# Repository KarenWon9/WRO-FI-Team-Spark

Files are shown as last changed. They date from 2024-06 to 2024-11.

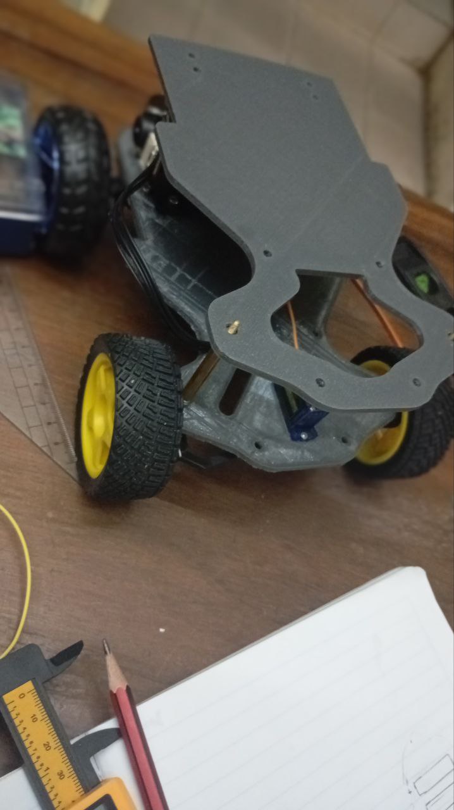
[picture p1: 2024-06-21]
other/First robot/Assembly.jpg

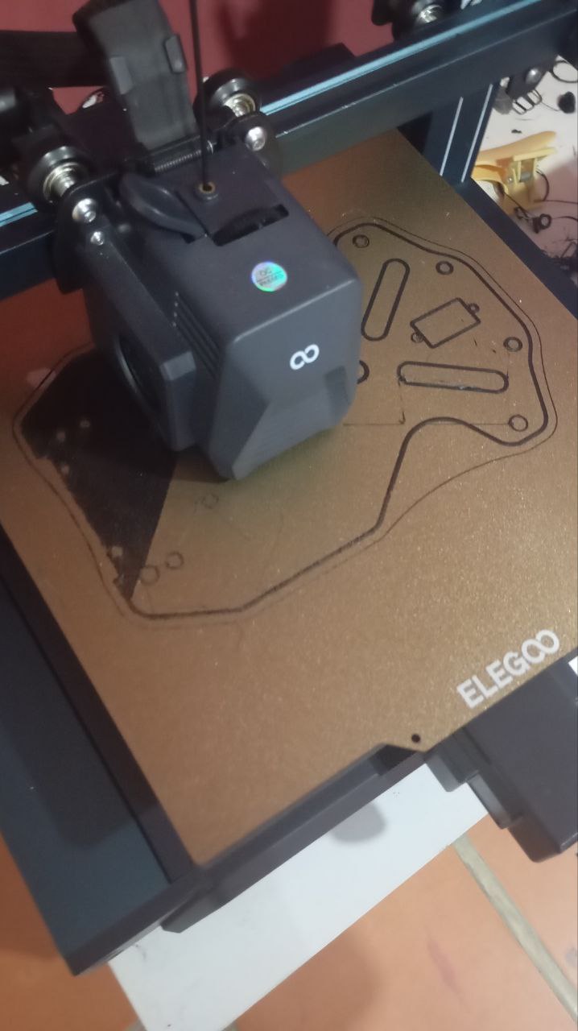
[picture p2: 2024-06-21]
other/First robot/Printig first chasis.jpg

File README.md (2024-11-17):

# Index

- 1.[ Introduction](#introduction)
    -
- 2.[ Components](#components)
    -
    - [Materials List](#materials-list)
    - [Arduino mega](#arduino-mega)
    - [Servo motor MG90S](#servo-motor-mg90s)
    - [Bridge H (L293N)](#bridge-h-l293n)
    - [Pixy2 cam](#pixy2-cam)
    - [Ultrasonic sensor (HC-S04)](#ultrasonic-sensor-hc-s04)
    - [Battery and charger](#battery-and-charger)
    - [Motor GA37-520](#motor-ga37-520)
    - [LM2596 HW-411 Step down](#lm2596-hw-411-step-down)

- 3.[ Robot floors](#robot-floors)
    -
    - [First and Second Floor](#first-and-second-floor)
        - [Front axel](#front-axle)
        - [Back axel](#back-axel)

    - [Third floor](#third-floor)
    - [Fourth floor](#fourth-floor)
        
- 4.[ 3D desing](models/)
    -
    - [Parts list](models/README.md#parts-list)
    - [Printing settings and recommendations](models/README.md#printing-settings-and-recommendations)
    - [STL files](models/stl/)
    - [Files ready to print](models/ready%20to%20print/)
    - [Full Chasis](models/Full%20chassis%20turkey.step)

- 5.[ Circuit diagram](schemes/README.md#circuit-diagram)<!--[Carpeta de Fuentes](../) asi se puede hacer un enlace con una carpeta -->
    -

- 6.[ Codes](src/)
    -
    - [Open challenge](src/Open%20challenge.ino)
    - [Closed challenge](src/Closed%20challenge.ino)

- 7.[ Flowcharts](src/README.md#flowcharts)
    -
    - [Open challenge](src/README.md#open-challenge)
    - [Closed challenge](src/README.md#close-challenge)
    
- 8.[ Vehicle photos](v-photos/README.md)
    -

- 9.[ Performance videos](video/README.md)
    -
    - [Open challenge](video/README.md#open-challenge)
    - [Closed challenge](video/README.md#closed-challenge)

- 10.[ Team photos](t-photos/)
    -
    - [Official photo](t-photos/README.md#official-photo)
    - [Funny photo](t-photos/README.md#funny-photo)

- 11.[ Annex](other/)
    -
    - [First robot](other/First%20robot/)
    - [Second robot](other/Scond%20robot/)
    - [Thirt robot - Final](other/Third%20robot%20-%20Final/)

<!---------------------------------------------espanol-------------------------------------------------------- -->

# Introduction 
Spark is a team from the Salto Angel School participating in the World Robot Olympiad 2024 (WRO) in the future engineers’ category. This team is comprised of three students: Victoria Saez, the new Captain who is in charge of the programming and electronic parts; Sebastian Salina, who is responsible for the designing and mechanical parts of the robot; and finally, Rosa Wong, who attends the documentation and is also a university student at Rafael Urdaneta University.

The World Robot Olympiad (WRO) is an event where young people from different parts of the world meet to show their knowledge and abilities in diverse categories. The future engineers' category is based on the creation of an autonomous robot capable of driving around a game field that measures 3m x 3m using obstacles in it or without them. Every year, the rules and challenges partially change and every four or five years represents a different challenge.

This report explains the components and parts of the robot built and designed by Team Spark to afford all the competition`s challenges.

# Components

## Materials List

| **Pieces** | **Quantity** |
|---|---|
| Arduino Mega | 1 |
| Pixy2 Cam | 1 |
| Ultrasonic Sensor (HC-SR04) | 3 |
| Bridge H L298N | 1 |
| Pull-up Button | 1 |
| Motor GA37-520 of 320rpm | 1 |
| Servo Motor MG90S | 1 |
| NI-MH Battery 12V 3000mAh | 1 |
| LM2596 HW-411 Step Down | 2 |
| Switch button | 1 |

## Arduino mega

(https://postimg.cc/2bnQkcR0)

| | | | |
| --- | --- | --- | --- |
| **Microcontroller** | ATmega2560 | **Operating Voltage** | 5V |
| **Input Voltage** | 7-12V | **Digital I/O Pins** | 54 (15 provide PWM output) |
| **Analog Input Pins** | 16 | **Flash Memory** | 256 KB |
| **SRAM** | 8 KB | **EEPROM** | 4 KB |

A unique controller, the Arduino Mega, was chosen to
manage all the robot`s functions. This model is distinguished
by its great prosecution capability inside the Arduino family,
letting it sort out complete code and manage a wide range of
components thanks to its large quantity of digital pins,
analogic, and PWM.

## Servo motor MG90S
(https://postimg.cc/4Y5NgpSp) 1-2-4-5-10-20pcs-MG90-S-Micro-Servo-Motor-Metal-Gear-Analog-RC-Servomotor-180-jpg.jpg (https://postimg.cc/SjMSKBPS)

| | | | |
| --- | --- | --- | --- |
| **Weight** | 13.4g  | **Operating speed**  | 0.1 s/60 degree, 0.08 s/60 degree (6V) 
| **Dimension** | 22.5 x 12 x 35.5 mm | **Operating voltage**| 4.8 V - 6.0 V |
| **Stall torque**  | 1.8 kgf·cm (4.8V), 2.2 kgf·cm (6V) | **Dead band width** | 5 μs |

It uses the servomotor MG90S in the turning system to get
precise turns. This model is smaller, lighter, and offers higher
torque than the SG90, which allows it to move the wheels with
the necessary strength for shunting, mainly in obstacle
evasion.

### Code

To make easier its use, we employed the library `<Servo.h>` and created a variable
called `SERVOPIN` where we put the pin that is in use, in this case, it is the 9.

``` ino
#include <Servo.h> // Library to control servomotors.

#define SERVOPIN 9 // Define the pin for the servomotor.

#define TURNGRADE 30 // Define the turning grades for the correct direction
#define CENTERVALUE 90 // Center value for the servomotor (straight).
#define MAXLEFT 156 // Top value towards the left for the servomotor.
#define MAXRIGHT 5 // Top value towards the right for the servomotor.

Servo direction; // Create an instance of the servomotor.

void center() {
  if (DEBUG) Serial3.println("Center"); // Print "Center" if DEBUG is active.
  direction.write(CENTERVALUE); // Place the servomotor in the central value (90 degrees).
}

void turnLeft() {
  if (DEBUG) Serial3.println("Left"); // Print "Left" if DEBUG is active.
  direction.write(MAXLEFT); // Turn the servomotor at the top to the left.
  direction.write(MAXLEFT); // Repeat the writing with precision.
  setMove(500, 1, TURNSPEED); // Perform the movement with 500 ticks in direction1 (forward) to TURNSPEED.
  center(); // Center the servomotor after the turning.
  stop(); // Stop the movement.
}

void turnRight() {
  if (DEBUG) Serial3.println("Right"); // Print "right" if DEBUG is active.
  direction.write(MAXRIGHT); // Turn the servomotor at the top to the right
  direction.write(MAXRIGHT); // Repeat the writing with precision.
  setMove(760, 1, MAXSPEED); // Perform the movement with 760 ticks in direction1 (forward) to MAXSPEED.
  center(); // Center the servomotor after the turning.
  stop(); // Stop the movement.
}

void turnGrade(int grade) {
  if (DEBUG) Serial3.println("turnGrade " + String(CENTERVALUE + grade)); // Print the calculated turn angle.
  direction.write(CENTERVALUE + grade); // Adjust the servomotor angle according to the specify grade.
}

```

This servomotor is used the whole time to perform the turnings that are required
during the challenges.

## Bridge H (L293N)
(https://postimg.cc/zyyJFzjQ)

| | | | |
| --- | --- | --- | --- |
| **Number of outputs**  | 4  | **Output current per channel**  | 2A - 3A peak|
| **Working voltage** | 5V to 35V  | **Current consumption (logical)** | 36mA  |

The L293N acts as an entrepreneur between the Arduino Mega and the motor, translating the instructions into movements. Its power to manage high voltages lets us use motors with nominal voltage, without limiting the controller voltage, which increases the efficiency and potential of the robot.

## Pixy2 cam
(https://postimg.cc/Jysw2JVr)

| | | | |
| --- | --- | --- | --- |
| **Procesador** | NXP LPC4330, 204 MHz, dual core | **Imagen sensor** | Aptina MT9M114, 1296×976 |
| **Field of view horizontaL** | 60° | **Field of view vertical** | 40° |
| **Operating current** | 140 mA | **Operating voltage** | USB (5V) o 6V a 10V |
| **RAM** | 264Kb | **Flash** | 2Mb |
| **Buses** | UART serial, SPI, I2C, USB, digital, analog | **Light** | 20 lumens approx |

The camera is capable of detecting seven colors
simultaneously. It is equipped with an internal processor,
which lets us explore just the necessary information for the
Arduino or other controllers due to the variety of connections
that allow it. Moreover, it counts with an obturation speed of 60 fps, an excellent gap, and white adjustable LED lights;
thus, the continuous movement and the lower light don’t
represent a huge problem.

### Code

#### Open challenge
With the camera connected to the pins I2C of the Arduino Mega add the library
`<Pixy2.h>`. we create a variable called `firstColorDetected` to save the first color that
is detected and apart a variable called `colorDetected` to indicate if any color is
detected. To start the camera pixy2 uses a `pixi.init()`, in the light of an additional
light is needed for the perception of the colors we will implement the
`pixy.setLamp(1, 0)` command, this will activate the camera LED lights.

``` ino
#include <Pixy2.h> 

Pixy2 pixy; // Create an object of the Pixy2 camera.

byte firstColorDetected = NONE; // Variable to save the first detected color.
bool colorDetected = false; // Indicate if a color is detected.

void flash(byte time) { //Function for indicating that the start button can be pressed 
  for (byte i = 0; i < time; i++) {
    pixy.setLamp(1, 0); // turn on the Pixy2 camera LED. 
    delay(200); // Delay 200 ms
    pixy.setLamp(0, 0); // turn off the Pixy2 camera LED
    delay(200); // Delay 200 ms
  }
}
In the case of the first color detected is blue which is assigned previously as 1, calls the function turnLeft.

           if (pixy.ccc.numBlocks > 0) { // if the Pixy detects an object
      stop(); // Stop the robot
      center(); // Center the servomotor.
      switch (pixy.ccc.blocks[0].m_signature) { // Depending on the signature of the object.
        case BLUE: // If detect a blue object.
          Serial3.println("BLUE"); // Print "BLUE" in the serial monitor.   
          if (!colorDetected) { // if any color has not been detected previously.
            colorDetected = true; // Mark color detected
            firstColorDetected = BLUE; // Stablish the color detected as blue.
          }
          if (colorDetected && firstColorDetected == ORANGE) { // if orange has already been detected.
            Go to orange; // Jump to the orange color section.
          }
Blue: // Tag the blue object.
          center(); // Center the servomotor
          readDistance(currentPosition); // Update 'currentPosition'
          readDistance(lastPosition); // Update 'lastPosition'
          while ((currentPosition[3] < 100)) { // While the left distance is less than 100 cm
            followLine(SPEED2); // Follow the wall to 'SPEED2'.
            readDistance(currentPosition); // Update 'currentPosition'
          }
         turnLeft(); // Turn to the left
          moveCM(40, 1, MAXSPEED); // Move the robot 40 cm forward to high-speed. 
          do {
            followLine(MAXSPEED); // Follow the inner walls to top-speed
            readDistance(currentPosition); // Update 'currentPosition'
          } while (currentPosition[3] > 100); // Repeat while the left distance is more than 100 cm
          break;

```

In the case of the first color detected being orange, assign it as 2 in the camera, and call the turnRight function.

``` ino
 case ORANGE: // If detect an orange object.
          Serial3.println("ORANGE"); // Print "ORANGE" in the serial monitor
          if (!colorDetected) { // If any color has not been detected previously.
            colorDetected = true; // Mark color detected
            firstColorDetected = ORANGE; // Stablish the first color detected as orange 
          }
          if (colorDetected && firstColorDetected == BLUE) { // If blue has already been detected.
            go to blue; // Jump to the blue color section. 
          }
Orange: // Tag the orange object.
          center(); // Center the servomotor.
          readDistance(currentPosition); // Update 'currentPosition'
          readDistance(lastPosition); // Update 'lastPosition'
          while ((currentPosition[2] < 100)) { // while the right distance is less than 100 cm
            followLine(SPEED2); // Follow the inner wall to 'SPEED2'
            readDistance(currentPosition); // Update 'currentPosition'
          }
          turnRight(); // Turn to the right.
          moveCM(40, 1, MAXSPEED); // Move the robot 40 cm forward to high-speed.
          do {
            followLine(MAXSPEED); // Follow the inner Wall to top-speed. 
            readDistance(currentPosition); // Update 'currentPosition'
          } while (currentPosition[2] > 100); // Repeat while the right distance is more than 100 cm
          break;
      }

```

## Ultrasonic sensor (HC-S04)
(https://postimg.cc/FYLFY2zg)

| | | | |
| --- | --- | --- | --- |
| **Operating voltage** | 5 V  | **Operating current** | 15mA |
| **Minimum range** | 2cm  | **Max. distance**  | 4m |
| **Measuring angle** | 15°  | **Output Echo signal**  | 40Hz |
| **Input Trigger signal**  | Input 10μs TTL | **Pulso Echo** | Output 100-25000 μs TTL |

The ultrasonic sensors are essential in our robot because
let's calculate distances by using ultrasonic vibes. These
sensors own a transmitter that sends the vibe and a receiver
to detect the echo of the reflexive vibes which lets us
determine the distance by the time it takes to come back with
a maximum detection of 4 meters, these sensors are ideal for
the game field size, which measures 3m x 3m. thanks to
them, the robot has a higher perception of its position and
anticipate possible coalitions effectively.

### Code

 To facilitate the frequency conversion of the Vibes reception in cms, use the library `<Ultrasonic.h>` and subsequently, define each sensor pin with Ultrasonic and the name given to the sensor followed by the (Trig, Echo).
``` ino
#include <Ultrasonic.h> // Library to manage ultrasonic sensors.
#define USTRIGHT A13 // Define the signal pin for the right ultrasonic sensor.
#define USERIGHT A12 // Define the echo pin for the right ultrasonic sensor.
#define USTLEFT A14 // Define the signal pin for the left ultrasonic sensor.
#define USELEFT A15 // Define the echo pin for the left ultrasonic sensor.

Ultrasonic USRight(USTRIGHT, USERIGHT); // Instance for the right ultrasonic sensor.
Ultrasonic USLeft(USTLEFT, USELEFT); // Instance to for left ultrasonic sensor.

int firstPosition[4]; // Array to upload the first position detected. 
int lastPosition[4]; // Array to upload the last position detected.
int currentPosition[4]; // Array to upload the current position detected.
int tempPosition[4]; // Array to upload the temporary position detected.

void readDistance(unsigned int* array) {
  array[2] = USRight.read(); // Upload the distance measure by the right ultrasonic sensor.
  array[3] = USLeft.read(); // Upload the distance measure by the left ultrasonic sensor.
}
```

Considering the values of the firstPosition, lastPosition, currentPosition and tempPosition, the robot does an angle correction to evade collisions both with the outer and inner wall staying centered.

``` ino
if (DEBUG2) printDistance(currentPosition); // Print the distances if DEBUG2 is active.
  if (tempPosition[2] < tempPosition[3]) { // If the right distance is less than the left position
    grade = map(currentPosition[2], tempPosition[2] - LMIN, tempPosition[2] + LMIN, TURNGRADE, -TURNGRADE); // Map the angle correction to the right.
    if (DEBUG) Serial3.println("1 Actual: " + String(currentPosition[2]) + ". Inicial: " + String(tempPosition[2])); // Depuration
  } else { // If the left distance is less or equal to the right 
    grade = map(currentPosition[3], tempPosition[3] - LMIN, tempPosition[3] + LMIN, -TURNGRADE, TURNGRADE); // Map the angle correction to the left.
    if (DEBUG) Serial3.println("2 Actual: " + String(currentPosition[3]) + ". Inicial: " + String(tempPosition[3])); // Depuration
  }
 if (DEBUG) Serial3.println("Grades : " + String(grade)); // Print the angle calculated correction.
  if (grade > TURNGRADE) { // Limit the higher turning angle.
    grade = TURNGRADE;
  } else if (grade < TURNGRADE * -1) { // Limit the lower turning angle
    grade = -TURNGRADE;
  }

```

## Battery and charger
(https://postimg.cc/pmzxWzcs) (https://postimg.cc/qgqTt9Zh)

| | | | |
| --- | --- | --- | --- |
| **Voltage**  | 12V  | **Capacity** | 3000mAh  |
| **Weight** | 567g | **Connector** | XT30 |
| **Replaceable Fuse** | 20A ATM | | |

After an extensive period of using NI-MH Batteries, we
have chosen a 12V battery and 3000 mAh Rev Robotics. This
new battery offers significant advantages.

Firstly, it gives better autonomy, letting the robot work
through longer periods without the charging needs. Its 12
voltages are enough to completely provide the energetic
needs of the robot, ensuring a favorable performance.

In addition, the battery includes a versatile charger with
two charging modes; a lower one (0.9 A) and a faster one (1.8
A), allowing flexibility in the time charging. Also, it is allowed
on international trips by airplane because it is made with
nickel which is safe for its transport.

Lastly, it is a prefabricated battery and offers a superior
level of security and efficiency as compared to the settings of
individual batteries.

## Motor GA37-520
(https://postimg.cc/xcWJpGb5) 

| | | | |
| --- | --- | --- | --- |
| **Nominal voltage**  | 12V | **Rated power** | 8,3W |
| **Rated current**| 1,5A | **Reduction** | 18.8:1  |
| **No-load speed** | 320rpm | **Rated speed**| 224rpm  |
| **No-load current** | ≥120mA | **Rated current**  | ≥400mA |
| **Rated torque** | 3.1Kg.cm  | **Par nominal**  | 0.67Kg.cm |

From a robotic kit, we have obtained two motors. Each one
to 12V, they are capable of going at a nominal speed of
250rpm and a 3,5 kg torque. Therefore using just a 12V motor
is enough to give it the speed, control, and attraction needed,
as well as greater management thanks to its encoder which
Let us have better precision in the turns that the robot should
do in the game field.

### Code

#### Open challenge

Firstly, we defined the variables that go in the H bridge and at
the same time connected the motor that is called `IN1` and IN2,
equally, we defined 3 different speeds (`MAXSPEED`,
`TURNSSPEED`, `SPEED2`) that could be inside of a range
between 255 and 0.

``` ino
#define IN1 4 // Define IN1 to the motor control pin.
#define IN2 5 // Define IN2 to the motor control pin.

#define MAXSPEED 250 // Top-Speed of the motor.
#define TURNSPEED 180 // Turnings Speed.
#define SPEED2 140 // Secundary Speed.

void stop() {
  if (DEBUG) Serial3.println("Stop"); // Print "Stop" in the serial monitor if the mode depuration is active.
  digitalWrite(IN1, LOW); // Turn off the motor in the IN1 direction.
  digitalWrite(IN2, LOW); // Turn off the motor in the IN2 direction.
}

void forward(byte speed) {
  if (DEBUG2) Serial3.println("Forward " + String(speed)); // Print "Forward" and the speed if DEBUG2 is active.
  analogWrite(IN1, speed); // Assign the speed in IN1 to go forward.
  digitalWrite(IN2, LOW); 
}
void backward(byte speed) {
  if (DEBUG) Serial3.println("Backward " + String(speed)); // Print "Backward" and the speed if DEBUG is active.
  digitalWrite(IN1, LOW); // turn off IN1 to return
  analogWrite(IN2, speed);

}
```

## LM2596 HW-411 Step down
(https://postimg.cc/LYcFFskc)

| | | | |
| --- | --- | --- | --- |
| **Input** | 4.5-40VDC | **Output** | 1.5-35VDC |
| **Rated Current** | 2A (Surge 3A) | **Regulation** | 0.5% |

To protect the robot`s electronic components from
possible damages caused by higher voltages that are not
required, for this, we have incorporated a voltage regulator in
our system. This device assures a constant and stable energy
supply, which prevents failures in the components, and also
increases the stability and movement of the robot in its
performance.

# Robot floors
The robot is made up of four floors
listed from button to top.

## First and Second Floor
Both floors are connected themselves including the Steering system and the Driving
system.

### Front Axle
The front axle of our robot is located in a steering system boosted by a servo
(Mg90s). this system counts with two wings, a superior one and a lower one, that
allow an appropriate Caster, between the wings we can find the pivots that count
with two bearings that facilitate the free movement of the wheels and avoid an
incorrect Camber, both pivots include a steering arm which is connected through
the Tie Rod.

Movement transmission is carried out by the servo connected to the Tie Rod. This
is connected at the same time with the Steering Arm of the right Wheel to make the
movement transmission we use the Steering Linkage that is connected to the left
steering arm. The Tie Rod has a screw thread which allows an adjustable Toe. The
tire rod and the steering linkage count with the rod end at the ends give us a wide
work range. making it much easier to integrate the servo with the steering system.

### Back Alxe
In the back of the robot, we can find the driven system (the wheels and the motor).
This motor transmits the movement through a chain and two sprockets a small one
with 10 teeth that is connected to the shaft and the bigger one with 15 teeth which
is connected to the motor. in this setting the velocity increases x1.5, resulting in a
rated speed of 540RPM. also, the ring for the wheels was modified to fit with a
5mm hexagonal shaft, which makes the movement transmission and the assembly
easier.

## Third Floor.
On the third floor, the robot has different electronic components that are essential. It is located the battery which provides the needed energy to the proper function of the robot. As well as the camera that let get images and detect obstacles. Besides, the ultrasonic sensors and the laser sensor are included, and each one sets in its respective support that helps with its positioning and functioning.

## Fourth floor.
On the fourth robot`s floor is located the controller and near it the shield, which organizes all the electric connections, including the feeding. The connections are soldered, avoiding accidental disconnection, and minimizing the errors and accidents during the robot's manipulation.

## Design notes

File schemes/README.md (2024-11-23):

# Circuit diagram
(https://postimg.cc/Mf2J6gyz)

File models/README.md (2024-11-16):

# 3D desing

## Parts list
| Peace | Total |
|---|---|
| Front ring | 2 |
| Back ring | 2 |
| Pivot | 2 |
| Pivot shaft | 2 |
| Ultrasonic case pt1 | 2 |
| Ultrasonic case pt2 | 2 |
| Flexible wings | 2 |
| Pixy base | 1 |
| Laser sensor case pt1 | 1 |
| Laser sensor case pt2 | 1 |
| Chasis first floor | 1 |
| Chasis second floor | 1 |
| Chasis third floor | 1 |
| Chasis fourth floor pt1 | 1 |
| Chasis fourth floor pt2 | 1 |

## Printing settings and recommendations

In this explanation we use the original printing configurations implemented in the proyect, but there are parameters that depend on the material to be used. In the proyect we use PETG by sunlu, in addition to TPU by Eryone for the flexible parts in the chassis (the wings). You can modify this parameter depending on the material and the temperature of the ambient, the melting point of the material, and your 3D printer potential. in this case, we use the Elegoo Neptune 3 Pro.

All the files are distributed in an optimal positioning; this can say they are in a position ready to print when you insert them in the slicer (this time we use Ultimaker Cura) most of the pieces do not need support, except some pieces like the ultrasonicase pt 2 and the laser sensor pt1, But evaluating the configurations shows why it is recommended to use support in most of the pieces to increase the final resource, there are the recommended configurations for the pieces.

- Layer Height: 2 mm
- Recommended infill density: 35% 60% 
- Infil pattern: triangular (You can change the infill pattern)

- Printing speed: 
    - First layer: 10 mm/s
    - Outer wall 75 mm/s
    - Inner wall 90 mm/s
    - top/Bottom 75 mm/s

- Fan speed
    - regular speed 30%
    - Máximum speed 45%
    - Mínimum speed 10%
    - Initial speed 15%

- Support:
    - Support structure: Normal
    - Support overhang angle: 45°
    - Support pattern: zig zag
    - Support density: 25%-35%
    - Support placement: Touching build plate

- Used printing temperatures: 
    - PETG:
        - Nozzle: 255°
        - Build Plate: 105°
    - TPU
        - Nozzle: 220°
        - Build Plate: 70°

> [!NOTE]
> The only pieces that is totally necessary to print with supports like the Ultrasonic Case pt2 and Laser sensor case pt1, We recommend print the pieces in this configurations.

(https://postimg.cc/gwqnXT7M)

(https://postimg.cc/HrMJHx91)

> [!TIP]
> The recommended materials for this project are ASA and ABS for their mechanical properties, Temperature resistance and stability for this Kind of projects that requires mechanical stress and impact resistance.

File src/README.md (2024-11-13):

# Flowcharts

## Open challenge
(https://postimg.cc/0zhhw0jy)

## Closed challenge
(https://postimg.cc/V5HWc5Rd)

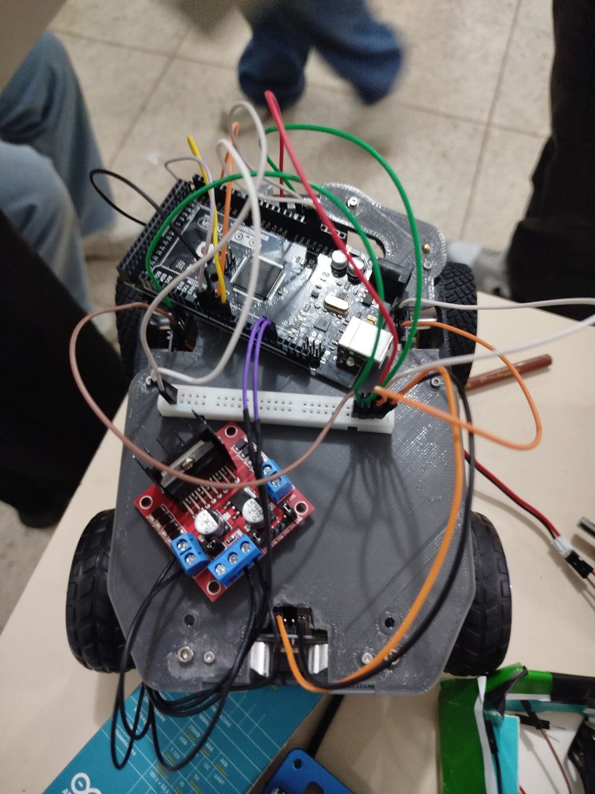
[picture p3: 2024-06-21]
other/First robot/Conections 2.jpg

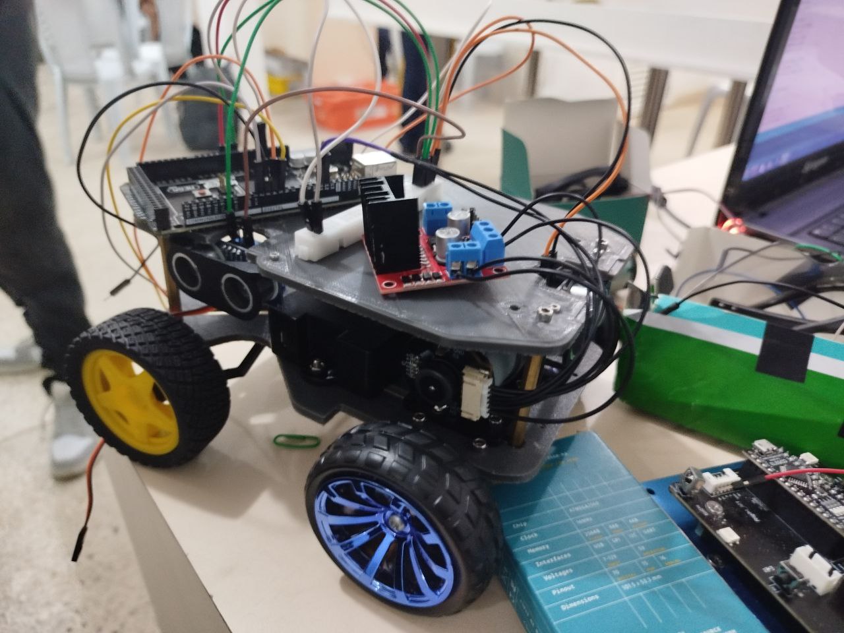
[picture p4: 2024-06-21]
other/First robot/Conections 3.jpg

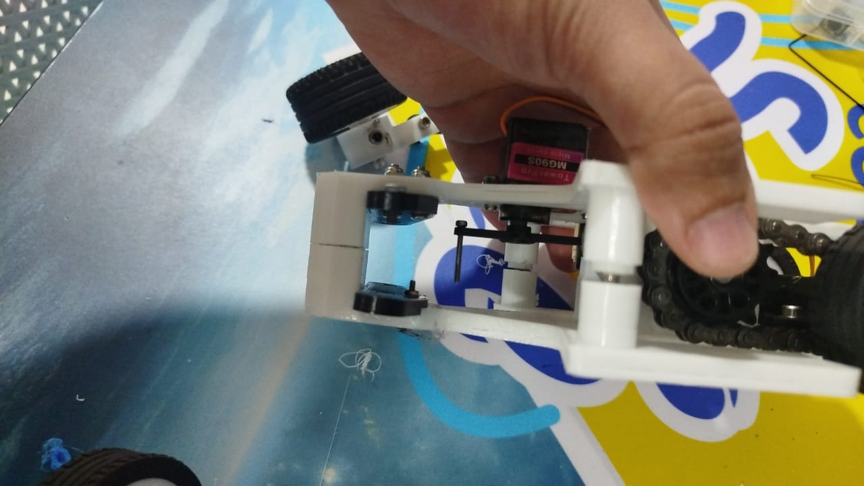
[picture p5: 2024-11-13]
other/Third robot - Final/Direction sistem 1.jpg

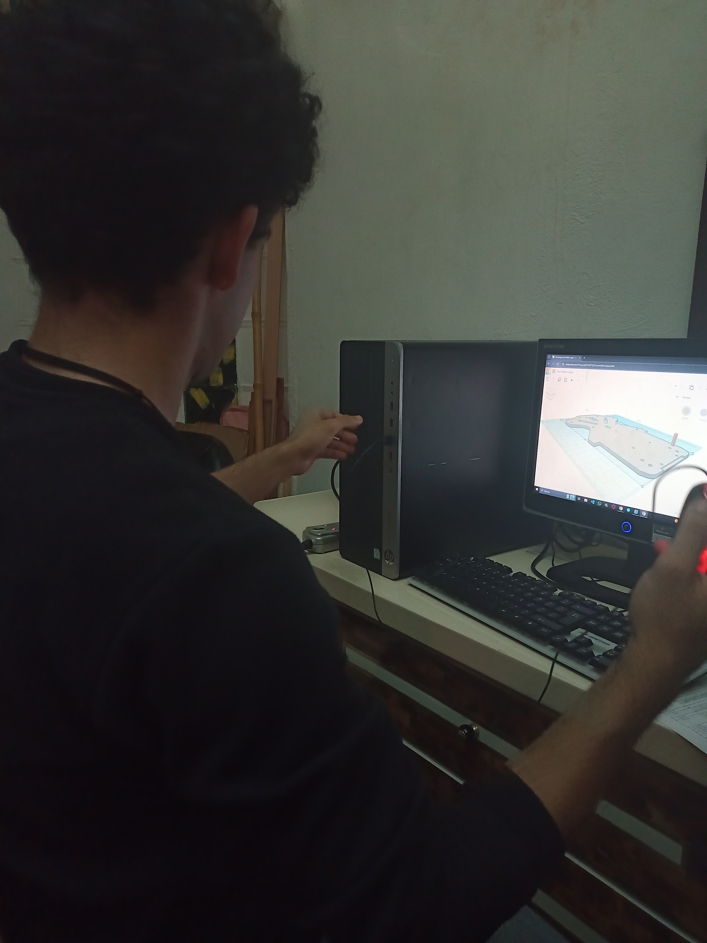
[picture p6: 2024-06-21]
other/First robot/Desingning in 3D.jpg

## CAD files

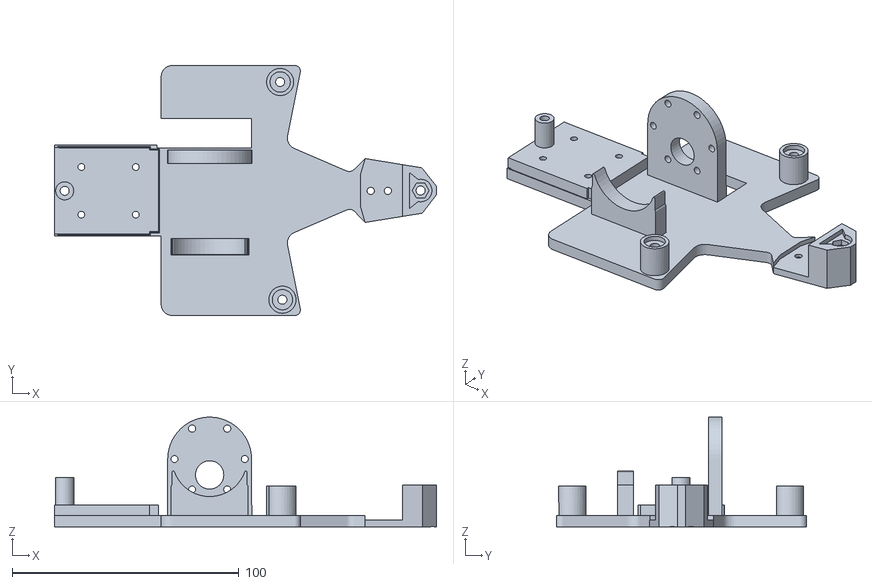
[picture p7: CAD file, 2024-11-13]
models/stl/chassis and steering/EN3PRO_chassis first floor .stl
168.5 x 110.3 x 48.3

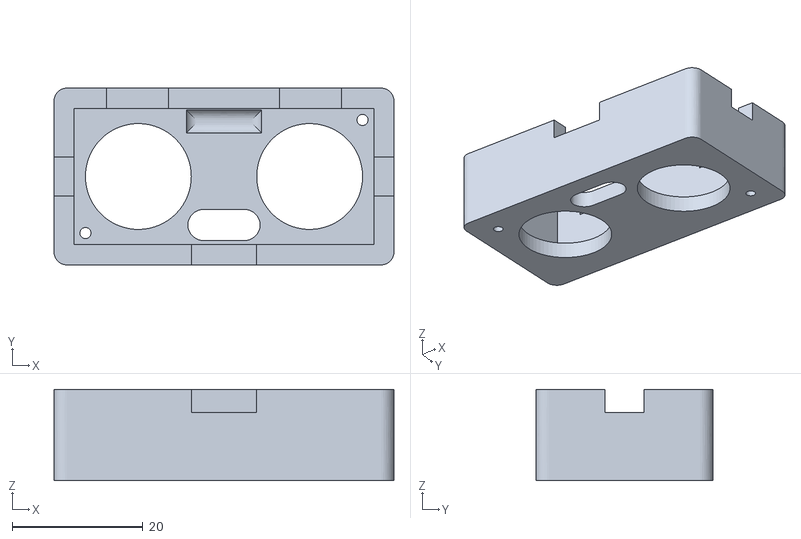
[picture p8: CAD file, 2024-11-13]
models/stl/sensors case and basis/EN3PRO_ultrasonic case Pt1.stl
52.0 x 27.1 x 14.0

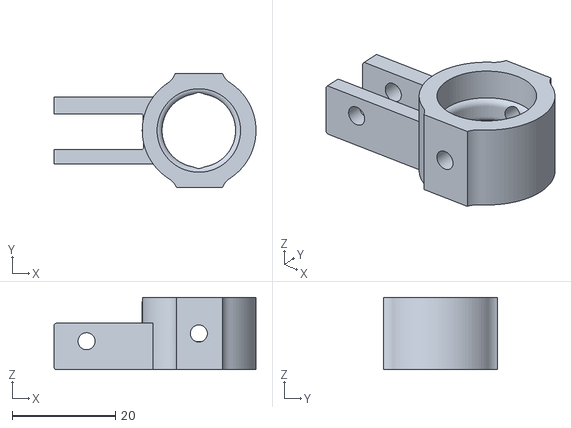
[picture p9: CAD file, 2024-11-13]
models/stl/chassis and steering/EN3PRO_pivot.stl
39.1 x 22.0 x 14.0

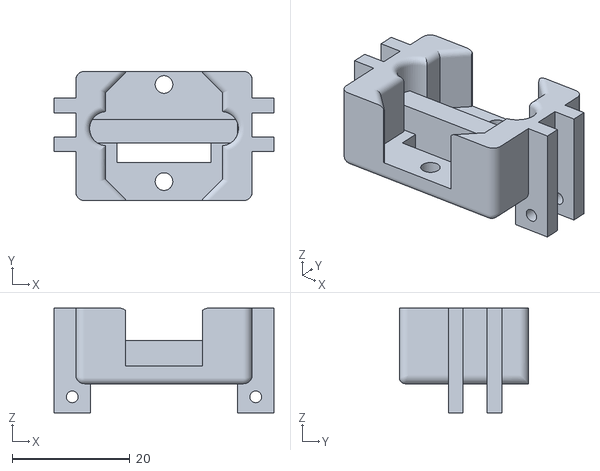
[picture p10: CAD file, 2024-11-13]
models/stl/sensors case and basis/EN3PRO_Laser sensor case pt1.stl
37.4 x 22.0 x 17.8

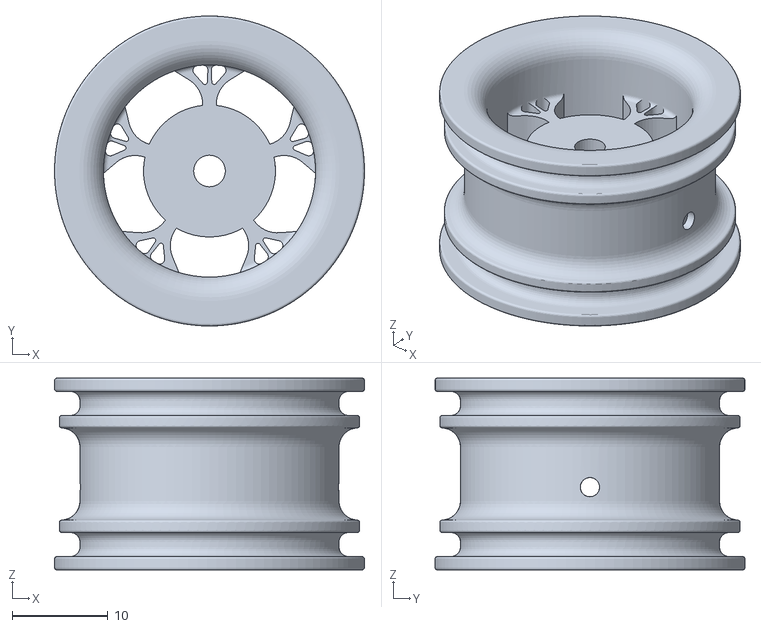
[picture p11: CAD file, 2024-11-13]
models/stl/chassis and steering/EN3PRO_Back Ring.stl
32.3 x 32.3 x 20.0

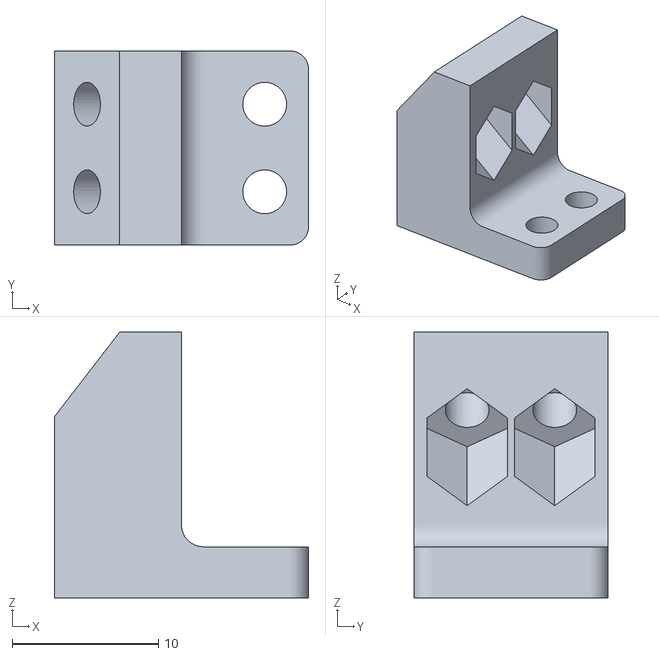
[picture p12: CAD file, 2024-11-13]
models/stl/sensors case and basis/EN3PRO_pixy basis.stl
17.4 x 13.3 x 18.2

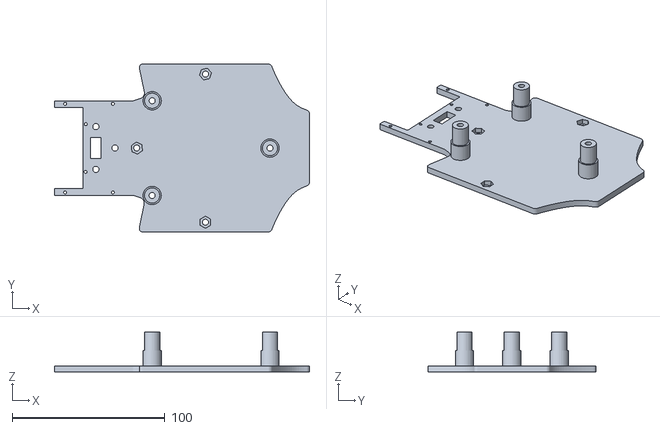
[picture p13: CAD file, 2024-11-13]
models/stl/chassis and steering/EN3PRO_chassis third floor .stl
166.9 x 109.9 x 26.0

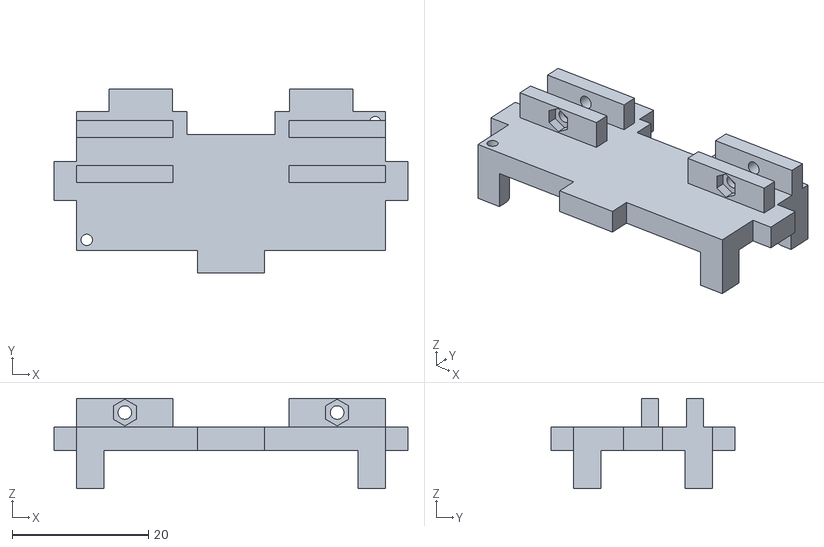
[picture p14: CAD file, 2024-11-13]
models/stl/sensors case and basis/EN3PRO_Ultrasonic Case Pt2.stl
52.0 x 27.1 x 13.3

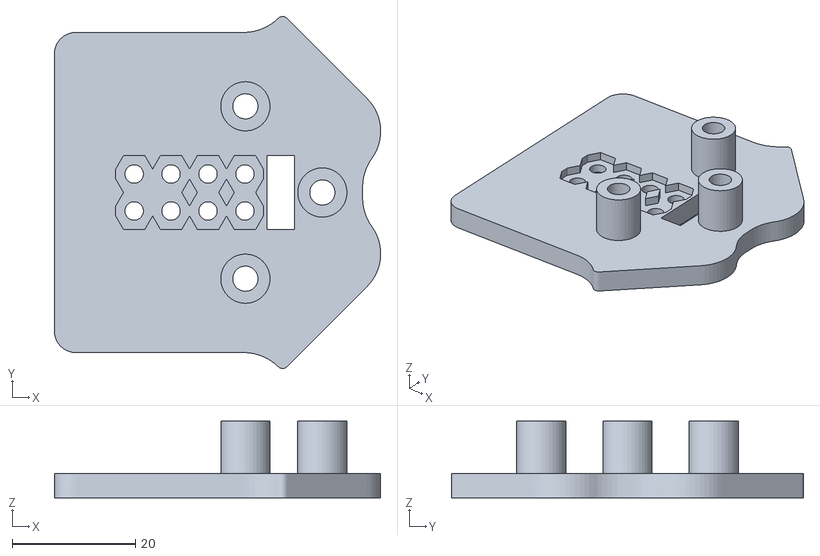
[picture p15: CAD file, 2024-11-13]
models/stl/chassis and steering/EN3PRO_Chassis fourth floor Pt2.stl
53.0 x 57.2 x 12.5

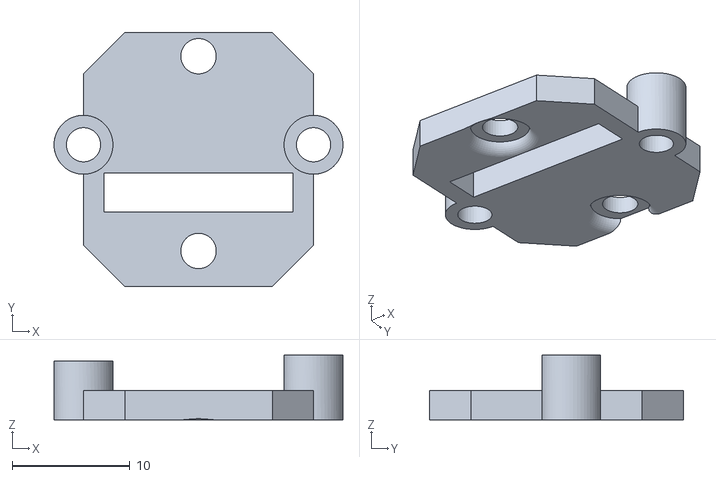
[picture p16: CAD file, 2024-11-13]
models/stl/sensors case and basis/EN3PRO_Laser sensor case pt2.stl
24.5 x 21.5 x 5.50

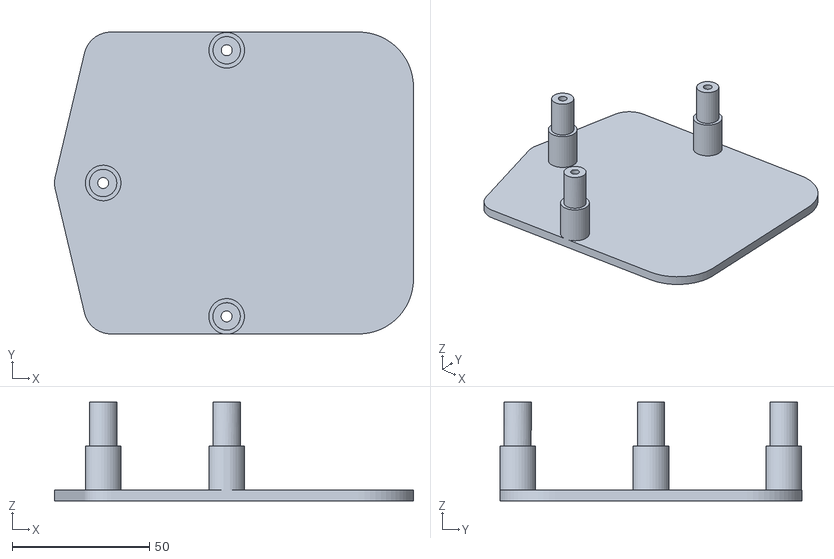
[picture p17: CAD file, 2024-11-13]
models/stl/chassis and steering/EN3PRO_chassis fourth floor p1.stl
130.8 x 110.0 x 36.0

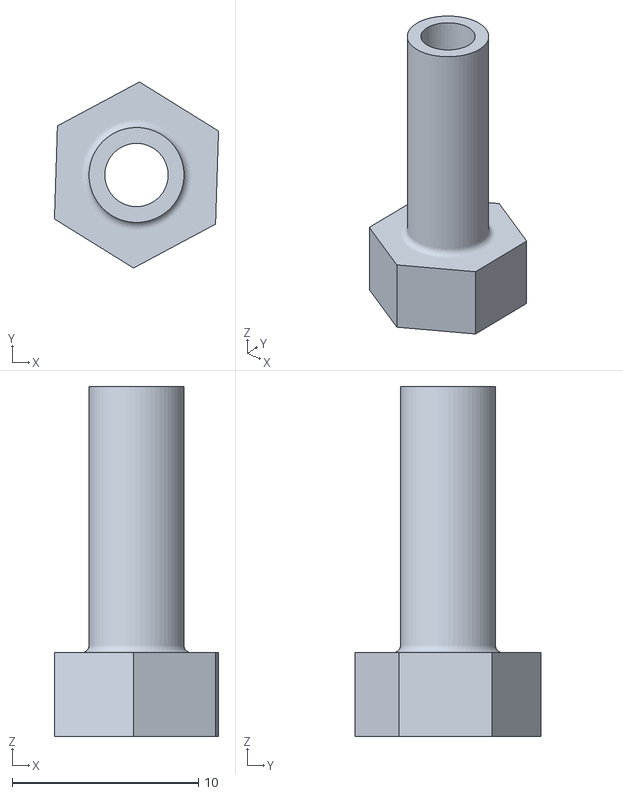
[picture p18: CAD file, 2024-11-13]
models/stl/chassis and steering/EN3PRO_pivot shaft.stl
8.82 x 9.99 x 18.8

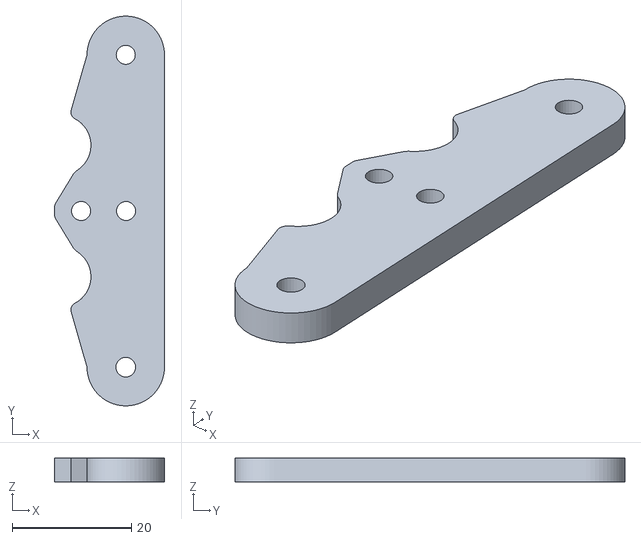
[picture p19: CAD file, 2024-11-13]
models/stl/chassis and steering/EN3PRO_flexible wings.stl
18.5 x 65.4 x 4.00

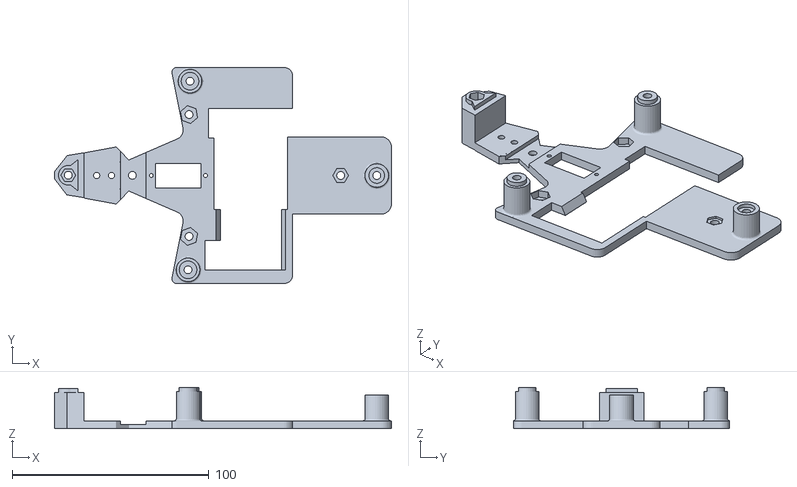
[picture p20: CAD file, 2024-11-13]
models/stl/chassis and steering/EN3PRO_chassis second floor.stl
171.5 x 110.0 x 21.0

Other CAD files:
models/stl/chassis and steering/EN3PRO_Front Ring.stl

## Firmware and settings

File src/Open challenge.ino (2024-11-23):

/*
Opening challenge code of the Team Spark, future Engineers’ category.
    Using Pixycam2.1 to detect blue and orange lines, ultrasonic sensor HC-SR04 
  To detect the left and right distance of the robot, sensor VL53L0X to detect frontal direction distance (no longer used in this code), servomotor mg90s to direct the robot, motor DC and Bluetooth module to the practices.
  (this will not be allowed during the competition according to the rules).
*/

#include <Servo.h> // Library to control servomotors.
#include <Pixy2.h> // Library to manage the Pixy2 camera.
#include <Wire.h> // Library for the I2C communication.
#include <DFRobot_VL53L0X.h> // Library to the VL53L0X distance sensor.
#include <avr/wdt.h> // Library to manage the watchdog timer.
#include <Ultrasonic.h> // Library to manage the ultrasonic sensors.

#define STARTBUTTON 18 // Define the start button pin.

#define IN1 4 // Define IN1 to the motor control pin.
#define IN2 5 // Define IN2 to the motor control pin.

#define LEDREADY 53 // Define the indicated control LED pin.
#define SERVOPIN 9 // Define the servomotor pin.
#define ENCODERPIN 2 // Define the encoder pin.
#define USTRIGHT 31// Define the signal pin to the right ultrasonic sensor.
#define USERIGHT 30 // Define the echo pin to the right ultrasonic sensor.
#define USTLEFT 45 // Define the signal pin to the left ultrasonic sensor.
#define USELEFT 44 // Define the echo pin to the left ultrasonic sensor.

#define TURNGRADE 30 // Define the turning grade to check the direction adjustment.
#define NEUTRO 0 // Define constant to the neutral state.
#define IZQUIERDA 1 // Define the constant in the left direction.
#define DERECHA 2 // Define the constant in the right direction. 
#define CENTERVALUE 90 // Center Value to the servomotor (Straight).
#define MAXLEFT 156 // Top-value towards the left for the servomotor.
#define MAXRIGHT 5 // Top-value towards the right for the servomotor.
#define MAXSPEED 250 // Top-speed of the motor.
#define TURNSPEED 180 // Speed for turnings.
#define SPEED2 140 // Secondary speed.

#define LMIN 10 // Low limit of the sensors reading. 
#define LMAX 10 // top limit of the sensors reading.
#define ENDLINE 20 // Limit the ending line.

#define NONE 0 // None color detected.
#define BLUE 1 // Blue color detected.
#define ORANGE 2 // Orange color detected.

#define DEBUG true // Define the depuration.
#define DEBUG2 false // Define the second depuration level.
#define SENSORCOUNT 1 // Define the sensor`s number VL53L0X.

Pixy2 pixy; // Create an instance of the Pixy2 camera.
Servo direccion; // Create an instance for the servomotor.
DFRobot_VL53L0X sensors[SENSORCOUNT]; // Create an array of sensors VL53L0X.
Ultrasonic USRight(USTRIGHT, USERIGHT); // Instance for the right ultrasonic sensor.
Ultrasonic USLeft(USTLEFT, USELEFT); // Instance for the left ultrasonic sensor.

int firstPosition[4]; // Array to upload the first position detected.
int lastPosition[4]; // Array to upload the last position detected.
int currentPosition[4]; // Array to upload the current position detected.
int tempPosition[4]; // Array to upload the detected position temporarily.

byte sentido = NEUTRO; // Variable to update the current position.
byte turnCount = 0; // Count the turnings done.

bool state = false; // State of the start button.
unsigned long encodeCounter = 0; // Count for the encoder pulls.
unsigned long readTime = 0; // Upload the time of the last reading of the sensors.
char myChar; // Variable to upload characters received.
const uint8_t xshutPins[SENSORCOUNT] = { 38 }; //Pin to enable or disenable the sensor VL53L0X.
byte firstColorDetected = NONE; // Variable to save the first color
detected 
bool colorDetected = false; // Indicate if a color is detected.

void stop() {
  if (DEBUG) Serial3.println("Stop"); // Print "Stop" in the serial monitor if the depuration mode is active.
  digitalWrite(IN1, LOW); // Turn off the motor in the IN1 direction. 
  digitalWrite(IN2, LOW); // Turn off the motor in the IN2 direction.
}

void forward(byte speed) {
  if (DEBUG2) Serial3.println("Forward " + String(speed)); // Print "Forward" and the speed if DEBUG2 is active.
  analogWrite(IN1, speed); // Assign the speed in IN1 to go forward.
  digitalWrite(IN2, LOW); 
}

void backward(byte speed) {
if (DEBUG) Serial3.println("Backward " + String(speed)); // Print "Backward" and the speed if DEBUG is active.
  digitalWrite(IN1, LOW); // turn off IN1 to go backward.

  analogWrite(IN2, speed);
}

void center() {
  if (DEBUG) Serial3.println("Center"); // Print "Center" if DEBUG is active.
  direction.write(CENTERVALUE); // Place the servomotor in the central value (90 degrees).
}

void turnLeft() {
  if (DEBUG) Serial3.println("Left"); // Print "Left" if DEBUG is active.
  direction.write(MAXLEFT); // Turn the servomotor at the top to the left.
  direction.write(MAXLEFT); // Repeat the writing with precision.
  setMove(500, 1, TURNSPEED); // Perform the movement with 500 ticks in direction1 (forward) to TURNSPEED.
  center(); // Center the servomotor after the turning.
  stop(); // Stop the movement.
}

void turnRight() {
  if (DEBUG) Serial3.println("Right"); // Print "right" if DEBUG is active.
  direction.write(MAXRIGHT); // Turn the servomotor at the top to the right
  direction.write(MAXRIGHT); // Repeat the writing with precision.
  setMove(760, 1, MAXSPEED); // Perform the movement with 760 ticks in direction1 (forward) to MAXSPEED.
  center(); // Center the servomotor after the turning.
  stop(); // Stop the movement.
}

void turnGrade(int grade) {
  if (DEBUG) Serial3.println("turnGrade " + String(CENTERVALUE + grade)); // Print the turn angle calculated.
  direction.write(CENTERVALUE + grade); // Adjust the servomotor angle according to the specify grade.
}

void initSensor() {
  Wire.begin(); // Start the I2C communication.

  for (uint8_t i = 0; i < SENSORCOUNT; i++) {
    pinMode(xshutPins[i], OUTPUT); // Set the sensor`s off pin as an output. 
    digitalWrite(xshutPins[i], LOW); // Turn off the corresponding sensor. 
  }

  for (uint8_t i = 0; i < SENSORCOUNT; i++) {
    pinMode(xshutPins[i], INPUT); // Set the sensor`s off pin as an input to restart the sensor.
    delay(10); // Delay 10 ms to restart the sensor
    sensors[i].begin(0x2A + (i * 2)); // Start the sensor with the specific I2C direction. 
    sensors[i].setMode(sensors[i].eContinuous, sensors[i].eHigh); // Set the continuous mode and the high precision.
    sensors[i].start(); // Start the sensor measurement.
  }
}

void readDistance(unsigned int* array) {
  array[0] = sensors[0].getDistance(); // Upload the distance measured by the frontal sensor.
  array[2] = USRight.read(); // Upload the distance measured by the right ultrasonic sensor.
  array3] = USLeft.read(); // Upload the distance measured by the left ultrasonic sensor.
}

void printDistance(unsigned int* array) {
  char buffer[6]; 
  for (byte i = 0; i < 4; i++) {
    sprintf(buffer, "%04d", array[i]);
    Serial3.print(buffer); 
    Serial3.print("    "); 
  }
  Serial3.println(); 
}

void flash(byte time) { //Function for indicating that the start button can be pressed 
  for (byte i = 0; i < time; i++) {
    pixy.setLamp(1, 0); // turn on the Pixy2 camera LED. 
    delay(200); // Delay 200 ms
    pixy.setLamp(0, 0); // turn off the Pixy2 camera LED
    delay(200); // Delay 200 ms
  }
}

void setMove(int tick, byte direction, byte speed) {
  unsigned long conteoActual = encodeContador + tick; // Calculate the final value of the encoder for the movement.
  if (DEBUG) Serial3.println("setMove " + String(tick)); 
  if (direction == 1) { 
    while (encodeContador < conteoActual) { // While the final encoder value is not reached.
      forward (speed); // Go forward to the specified speed. 
      if (DEBUG2) Serial3.println("Actual: " + String(encodeContador) + " Final: " + String(conteoActual)); 
      wdt_reset(); 
    }
  } else if (direction == 2) { // If the direction is backward
    while (encodeContador < conteoActual) { // While the final encoder value is not reached.
      backware(speed); // Go backward to the specified speed.      
if (DEBUG2) Serial3.println("Actual: " + String(encodeContador) + " Final: " + String(conteoActual)); 
      wdt_reset(); 
    }
  }
}

void moveCM(float distance, byte direction, byte speed) {
  unsigned int tick = int(distance * 1000.0 / 69.0); // Calculate the ticks in centimeters.
  setMove(tick, direction, speed); 
  wdt_reset();
}

void followLine(byte speed) {
  int grade = 0; // Define the variable 'grade' which represents the  angle correction.
  if (DEBUG2) Serial3.println("followLine"); 
  readDistance(currentPosition); // Read the distances and upload 'currentPosition'
  if (currentPosition[0] < 10) { // If the frontal distance is less than 10 millimeters
    stop(); // Stop the robot
    return; 
  }
  if (DEBUG2) printDistance(currentPosition); 
  if (tempPosition[2] < tempPosition[3]) { // If the frontal distance is less to the left
    grade = map(currentPosition[2], tempPosition[2] - LMIN, tempPosition[2] + LMIN, TURNGRADE, -TURNGRADE); // Map the angle correction to the right.   
 if (DEBUG) Serial3.println("1 Actual: " + String(currentPosition[2]) + ". Inicial: " + String(tempPosition[2])); 
  } else { // If the left distance is less or equal to the right 
    grade = map(currentPosition[3], tempPosition[3] - LMIN, tempPosition[3] + LMIN, -TURNGRADE, TURNGRADE); // Map the angle correction to the left.    if (DEBUG) Serial3.println("2 Actual: " + String(currentPosition[3]) + ". Inicial: " + String(tempPosition[3])); 
  }
  if (DEBUG) Serial3.println("Grados : " + String(grade)); 
  if (grade > TURNGRADE) { // Limit the top angle turning.
    grade = TURNGRADE;
  } else if (grade < TURNGRADE * -1) { // Limit the low angle turning.
    grade = -TURNGRADE;
  }
  if (DEBUG) Serial3.println("Grades : " + String(grade)); 
  turnGrade(grade); // Turn the servomotor to the angle calculated.
  turnGrade(grade); // Repeat the action to assure precision.
  moveCM(2, 1, speed); // Move the robot 2 cms forward at the specified speed 
}

void correctLeft() { //Function to correct the left distance.
  turnGrade(60); 
  moveCM(20, 1, MAXSPEED); 
  turnGrade(-66); 
  moveCM(20, 1, MAXSPEED); 
  turnGrade(0); 
  moveCM(20, 1, MAXSPEED); 
  stop(); 
}

void correctRight() { // Function to correct the right distance.
  turnGrade(-60); 
  moveCM(20, 1, MAXSPEED); 
  turnGrade(66); 
  moveCM(20, 1, MAXSPEED); 
  turnGrade(0); 
  moveCM(20, 1, MAXSPEED); 
  stop(); 

}

void goCar() {
  bool endCycle = false; // Define a variable for the block detection.
  Serial3.println("goCar"); 
  readDistance(tempPosition); 
  while (!endCycle) { 
    pixy.ccc.getBlocks(false, CCC_SIG_ALL, 2); // Request the Pixy detection of objects with any signature.
    readDistance(currentPosition); 
     if (pixy.ccc.numBlocks > 0) { // If the Pixy detects a block.
      stop(); // Stop the robot
      center(); // Center the servomotor
      switch (pixy.ccc.blocks[0].m_signature) { 
        case BLUE: // If detect a blue object.
          Serial3.println("BLUE"); 
          if (!colorDetected) { // if any color has not been detected previously.
            colorDetected = true; // Mark color detected
            firstColorDetected = BLUE; // Stablish the color detected as blue.       
 }
          if (colorDetected && firstColorDetected == ORANGE) { // If orange has already been detected.
            Go to orange; 
          }
azul: 
          center(); // Center the servomotor
          readDistance(currentPosition); // upload 'currentPosition'
          readDistance(lastPosition); // upload 'lastPosition'
          while ((currentPosition[3] < 100)) { // While the left distance is less than 100 cm.
            followLine(SPEED2); 
            readDistance(currentPosition); // Upload 'currentPosition'
          }
          turnLeft(); // turn to the left
          moveCM(40, 1, MAXSPEED); // Move the robot 40 cm forward to the top speed. 
          do {
            followLine(MAXSPEED); // Follow the inner walls at the top-speed.
            readDistance(currentPosition); // Update 'currentPosition'
          } while (currentPosition[3] > 100); // Repeat while the left distance is more than 100 cm
          break;

        case ORANGE: // If detect an orange object.
          Serial3.println("ORANGE"); 
          if (!colorDetected) { // If any color has not been detected previously.
            colorDetected = true; // Mark color detected
            firstColorDetected = ORANGE; // Stablish the first color detected as orange        
   }
          if (colorDetected && firstColorDetected == BLUE) { // If blue has already been detected. 
go to blue; // Jump to the blue color section
          }
orange: 
          center(); // Center the servomotor
          readDistance(currentPosition); // Update 'currentPosition'
          readDistance(lastPosition); // Update 'lastPosition'
          while ((currentPosition[2] < 100)) { // while the right distance is more than 100 cm.
            followLine(SPEED2); // Follow the wall to 'SPEED2'.
            readDistance(currentPosition); // Update 'currentPosition'
          }
          turnRight(); // Turn to the right.
          moveCM(40, 1, MAXSPEED); // Move the robot 40 cm forward to the top speed.
          do {
            followLine(MAXSPEED); // Follow the inner Wall to top-speed. 
            readDistance(currentPosition); // Update 'currentPosition'
          } while (currentPosition[2] > 100); // Repeat while the right distance is more than 100 cm
          break;
      }

      stop(); // stop the robot at the end of the block detection.
      endCicle = true; // closing cycle.
      return; 
    } else { // If a block is not detected.
      Serial3.println("None detection block"); 
      printDistance(currentPosition); 
      followLine(MAXSPEED); // Follow the inner wall at the top speed.   
 }
  }
}

void IRS() {
  state = !state; // State changes between true and false.
  while (!digitalRead(STARTBUTTON)) {} // holdup till the button is pushed.
}

void encoder() {
  encodeContador++; // Increase the encoder counter.
}

void setup() {
  wdt_disable(); 
  pinMode(STARTBUTTON, INPUT_PULLUP); 
  pinMode(ENCODERPIN, INPUT_PULLUP); 
  pinMode(LEDREADY, OUTPUT); 
  digitalWrite(LEDREADY, LOW); 
  stop(); // Call the 'stop' function.
  direccion.attach(SERVOPIN); 
  center(); // Center the servomotor 
  Serial.begin(115200); 
  Serial3.begin(9600); 
  initSensor(); 
  attachInterrupt(digitalPinToInterrupt(ENCODERPIN), encoder, RISING); // Set an interruption for the encoder
  attachInterrupt(digitalPinToInterrupt(STARTBUTTON), IRS, FALLING); // Set an interruption for the start button.
  pixy.init(); 
  wdt_enable(WDTO_2S); 
  flash(3); // Call the 'flash' function to let wink the PixyCam LED three times.
  pixy.setLamp(0, 0); // turn off the PixyCam LED.
  state = false; // Stablish the robot`s initial state as false. 
  Serial3.println(millis()); 
  while (!state) { 
    readDistance(firstPosition); // Read the distance of the sensors and upload 'firstPosition'
    readDistance(tempPosition); // Read the distance of the sensors and upload 'tempPosition'
    readDistance(currentPosition); // Read the distance of the sensors and upload 'currentPosition'
    printDistance(currentPosition); 
    wdt_reset(); 
  }
  if (DEBUG) Serial3.println("Iniciated"); 
  digitalWrite(LEDREADY, LOW); // Assure the prepering LED it`s off. 
  center(); // Center the servomotor
  doceVueltas(); // Call the 'doceVueltas' function to make 12 laps (three laps done)
  moveCM(20, 1, MAXSPEED); // Call the 'moveCM' function to move the robot 20 cm forward at the top-speed.
  center(); // Center the servomotor again
  stop(); // Stop the robot
}

int count = 0; // Corner counter.

void doceVueltas() {
  for (count = 0; count < 12; count++) { 
    wdt_reset(); 
    goCar(); // Call the 'goCar' function to move the robot forward.
    followLine(MAXSPEED); // Call the 'followLine' function to follow the inner wall at the top-speed
    followLine(MAXSPEED); 
    followLine(MAXSPEED); 
    center(); // Center the servomotor (adjust the steering of the robot)
    if (DEBUG) Serial3.println("Lap " + String(count + 1) + "successfully done"); 
    if (DEBUG) Serial3.println();
    if (DEBUG) Serial3.println(); 
  }
  stop(); // Stop the robot after 12 complete laps.
}

void loop() {
}

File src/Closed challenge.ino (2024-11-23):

// Inclusion of libraries
#include <Pixy2.h>
#include <Servo.h>
#include "Ultrasonic.h"
#include <avr/wdt.h>
#include <VL53L0X.h>

// Pins and constants definition
#define SERVOPIN 9
#define ENCODERPIN 2
#define USTRIGHT 45
#define USERIGHT 44
#define USTLEFT 31
#define USELEFT 30
#define IN1 4
#define IN2 5
#define STARTBUTTON 18
#define NONE 0
#define BLUE 1
#define ORANGE 2
#define RED 3
#define GREEN 4
#define MAGENTA 5
#define CENTERVALUE 80
#define MAXLEFT 130
#define MAXRIGHT 35
#define MAXSPEED 250
#define TURNSPEED 200
#define SPEED2 140
#define DEBUG true
#define DEBUG2 false
#define YVALUE 65
#define XVALUERED 100
#define XVALUEGREEN 225
#define ENDLINE 20
#define GRADETURN 10

// objects` Creating.
Pixy2 pixy;                 
Servo direction;          
VL53L0X sensor;           
Ultrasonic USRight(USTRIGHT, USERIGHT); 
Ultrasonic USLeft(USTLEFT, USELEFT);  

// Control Variables.
bool state = false;          
bool end = false;      
unsigned long readTime = millis(); 
unsigned long encodeContador = 0; 
byte secondColor = 0;        
byte count = 0;              
int grade = 0;              
int currentGrade = CENTERVALUE; 

// Sequence-position Variables. 
int firstPosition[4];
int lastPosition[4];
int currentPosition[4];
int tempPosition[4];

// Variables for the color detected.
byte firstColorDetected = NONE;  // 0 = none, 1 = blue, 2 = orange
bool colorDetected = false;      

// Function to wink the pixy LED 
void flash(byte time) {
  for (byte i = 0; i < time; i++) {
    pixy.setLamp(1, 0);  // Turn-on the LED
    delay(200);
    pixy.setLamp(0, 0);  // Turn-off the LED.
    delay(200);
  }
}

//Function to stop the robot.
void stop() {
  if (DEBUG) Serial3.println("Stop");
  digitalWrite(IN1, LOW);   
  digitalWrite(IN2, LOW);
}

// Function to move forward.
void forward(byte speed) {
  if (DEBUG2) Serial3.println("Forward " + String(speed));
  analogWrite(IN1, speed);  
  digitalWrite(IN2, LOW);
}

// Function to move backward.
void backward(byte speed) {
  if (DEBUG2) Serial3.println("Backward " + String(speed));
  digitalWrite(IN1, LOW);  
  analogWrite(IN2, speed);
}

// Function to move the robot with the encoder and direction 
void setMove(int tick, byte direction, byte speed) {
  unsigned long conteoActual = encodeContador + tick;
  if (DEBUG2) Serial3.println("setMove " + String(tick));
  
  if (direction == 1) {  // Move forward 
    while (encodeCounter < currentCount) {
      forware(speed);
      if (DEBUG2) Serial3.println("Actual: " + String(encodeCounter) + " Final: " + String(currentCount));
      wdt_reset();  // Restart the watchdog timer
    }
  } else if (direction == 2) {  // Mover backward
    while (encodeContador < currentCount) {
      backwaredspeed);
      if (DEBUG2) Serial3.println("Actual: " + String(encodeContador) + " Final: " + String(conteoActual));
      wdt_reset();  // Restart the watchdog timer
    }
  }
}

// Function to move the robot to a specific distance in centimeters. 
void moveCM(float distance, byte direction, byte speed) {
  unsigned int tick = int(distance * 1000.0 / 70.5); 
  setMove(tick, direction, speed);  // Call a setMove to move the robot
  wdt_reset();  // Restart the watchdog timer
}

// Function to read the distances of the ultrasonic sensors and the distance laser sensor.
void readDistance(unsigned int* array) {
  array[0] = sensor.readRangeContinuousMillimeters();  // Read the laser sensor distance.
  array[1] = USRight.read();  // Read the right ultrasonic sensor distance.
  array[2] = USLeft.read();   // Read the left ultrasonic sensor distance
}

// Function to print the distances read in the serial monitor. 
void printDistance(unsigned int* array) {
  char buffer[6];
  for (byte i = 0; i < 4; i++) {
    sprintf(buffer, "%04d", array[i]);
    Serial3.print(buffer);
    Serial3.print("    ");
  }
  Serial3.println();
}

// Function to center the robot direction.
void center() {
  if (DEBUG) Serial3.println("Center");
  direccion.write(CENTERVALUE);  // Stablish the servo in the central position.
}

// Function to turn the robot in a specific grade. 
void turnGrade(int grade) {
  if (DEBUG) Serial3.println("turnGrade " + String(CENTERVALUE + grade));
  currentGrade = CENTERVALUE + grade;  // Adjust the direction.
  direccion.write(currentGrade);  // Move the servo to the new direction.
}

// Function to let the robot move one step slower, adjusting the direction if it is necessary. 
void nextStep(byte direction) {
  int dif = 0;
  wdt_reset();  // Restart the watchdog timer
  readDistance(currentPosition);  // Read the current distances. 
  printDistance(currentPosition);  // Print the distances.
  grade = 0;
  if(currentPosition[1] > 80 || currentPosition[2] > 80) return;  // If there are near obstacles, don`t move.
  // Adjust the turning grades according to the different positions. 
  if (tempPosition[1] >= tempPosition[2]) {
    if(direction == 0){
      dif = abs(tempPosition[1] - currentPosition[1]);
    }else {
      dif = abs(tempPosition[2] - currentPosition[2]);
    }
    switch (direction) {
      case 0:
      case 1:
        if (dif > 100) return;
        break;
      case 2:
        if (currentPosition[2] < 80) return;
        break;
      case 3:
        if (currentPosition[1] < 80) return;
        break;
    }
    grade = map(dif, 0, 100, 0, 100);  // Map the difference to a grade value.

    Serial3.println("Difference 1: " + String(dif) + ". Grades: " + String(grade));

    if (tempPosition[2] > currentPosition[2]) {
      grade *= -1;
    }
  }
  turnGrade(grade);  // Adjust the robot`s direction. 
  setMove(5, 1, MAXSPEED);  // Move the robot forward.
}

// Function to turn the robot to the left.
void turnLeft() {
  if (DEBUG) Serial3.println("Left");
  stop();  // Stop the robot.
  readDistance(currentPosition);  // Read current distances.
  center();  // Center the direction.
  while (currentPosition[2] < 140) {
    nextStep(1);  // Move till it detects an appropriate distance. 
  }
  stop();
  direction.write(MAXLEFT);  // Adjust the direction to the left.   setMove(700, 1, MAXSPEED);  // Move the robot forward
  center();  // Center again the position.
  stop();
}

// Function to turn the robot to the right.
void turnRight() {
  if (DEBUG) Serial3.println("Right");
  stop();  // Stop the robot.
  readDistance(currentPosition);  // read the current distances.
  center();  // Center the direction.
  while (currentPosition[1] < 140) {
    nextStep(3);  // Move till it detects an appropriate distance. 
  }
  stop();
  direccion.write(MAXRIGHT);  // Adjust the direction to the right.
  setMove(700, 1, MAXSPEED);  // Move the robot forward
  center();  // Center again the direction. 
  stop();
}
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

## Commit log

2024-06-07 Corrección de títulos
2024-06-07 se agregó servomotor y motor
2024-06-07 Se creo la carpeta Diseños 3D
2024-06-07 Se agregaron diseños 3D
    [Engranaje de eje hexagonal.STEP, Incredible Lappi.stl, Porta Ultrasonido.STL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]
2024-06-09 se elimino el codigo, se modifico mecanica y se agrego nueva carpeta de electronica con la seleccion de los componentes
2024-06-10 Se agregaron recomendaciones de diseño 3D
2024-06-10 Se agregó el diagrama de cableado
2024-06-14 Se colocó nombre a los diseños 3d y fotos del robot.
    [Engraje de eje hexagonal.stl]
2024-06-14 Intento 2
    [Base de ultrasonido.STL, Base para porta pixy.stl, Chasis inferior.stl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]
2024-06-14 Se modificó elección de componentes
2024-06-21 Se renombraron las fotos de equipo y eliminaron fotos del robot
2024-06-21 Se creo la carpeta Fotos del robot
2024-06-21 Se agregaron fotos al README.md de Fotos del robot
2024-06-23 motor y sensor ultrasonido (jpg)
2024-06-23 Más informacion de componentes parte 1
2024-06-23 Más informacion de componentes parte 2
2024-06-23 Más informacion de componentes parte 3 (motor)
2024-06-24 Se agregaron nuevos diseños 3D
    [Back wheel adapter.stl, Chassis Down.stl, Chassis up.stl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]
2024-06-24 Se eliminaron viejos diseños 3D
    [Base de ultrasonido.STL, Base para porta pixy.stl, Chasis inferior.stl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]
2024-06-24 se renombraron los diseños 3D
    [Adaptador de rueda de atras.stl, Base de porta pixy.stl, Chasis abajo .stl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]
2024-06-24 Se renombraron diseños 3D, se agregó lista de componentes 3D usados y se cambion la descripción del servo motor
    [Adaptador de rueda de atras al eje hexagonal .stl, Chasis inferior.stl, Chasis superior.stl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]
2024-06-24 Se agregó lista de materiales electrónicos
2024-06-24 Se agregó lista de componentes
    [Chasis abajo .stl, Chasis arriba.stl]
2024-06-24 Se agregó diagrama de cableado
2024-06-24 Se elimió diagrama de flujo anterior
2024-06-24 Se agregó nuevo diagrama de cableado
2024-06-24 Se agregó diagrama de cableado al REAME.md y se hicieron correcciones ortograficas
2024-06-24 Se actualizó código de desafío abierto
2024-06-24 Se cambiaron los nombres de los videos
2024-06-24 Se eliminaron dos fotos de equipo y se renombraron dos videos
2024-06-24 Se subió ensamblaje de tren delantero.jpg
2024-06-24 se elimino ensamblaje de rueda 1 y diagrama de flujo
2024-06-24 Se agregaron fotoa al README.md de fotos del equipo
2024-06-24 Correción de fotos del equipo
2024-06-24 Correción de foto de equpio en README.md
2024-06-24 Se agregó diagrama de flujo
2024-06-24 Se agrego diagrama de flujo
2024-06-24 Se agrego diagrama de flujo a codigp
2024-06-24 Se agreó el vídeo de rendimiento en desafío abierto
2024-06-24 link de video de rendimineto
2024-07-11 Se renombraron carpetas y reorganizaron archivos
    [Adaptador de rueda de atras al eje hexagonal .stl, Base de porta pixy.stl, Chasis abajo .stl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]
2024-07-11 Se creo la carpeta stl
    [Adaptador de rueda de atras al eje hexagonal .stl, Base de porta pixy.stl, Chasis abajo .stl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]
2024-07-12 se modifico README.md de other
2024-07-12 se agrego descripcion de codigo de la camara pixy2
2024-07-12 Se agregaron imagenes de apoyo
2024-07-12 Se movieron las fotos y videos a la carpeta adicional
2024-07-12 Se agregaron fotos del sensor de color
2024-07-12 Se agregó video probando la pixy2 a la carpeta adicional
2024-07-12 se eliminó el diagrama de cableado
2024-07-12 Se acyualizó README.md y código de desafío cerrado
2024-11-23 Modified circuit diagram
2024-11-23 modified circuit diagram v2
2024-11-23 US pin change
